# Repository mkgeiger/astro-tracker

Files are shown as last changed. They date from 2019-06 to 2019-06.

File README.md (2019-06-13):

# High precision Astro Tracker with wireless GOTO

## Overview

The inspiration of this project founded in the combination of my two hobbies: astronomy and microcontroller projects. This projects describes building an equatorial mount stepper motor controller with GPS high precision star-, moon- and sun-tracking. A wireless GOTO control via Skysafari App and a webinterface for individual stepper motor settings is also implemented. The features for my needs are:
* GPS timebase for high precision tracking
* tracking of rectascension in stellar, lunar, solar and user defined speeds
* north and south hemisphere support
* wireless GOTO over WIFI supporting LX200 protocol from the Skysafari App
* stepper motor control for rectascension and declination axis including fast slewing for GOTO
* LED indication of fast slewing in action
* individual stepper motor settings over a webpage presented by a webserver
* autoguider port
* 12V power supply

## Hardware

### NodeMCU ESP32

I decided to take this microcontroller board because of its high power with 2 cores, 4 fast high precision couters and easy programming, WIFI and small form factor. Following GPIOs are used:

  Signal          | ESP32
  ----------------|-----------
  RA_PHASE1..4    | GPIO12..15
  DEC_PHASE1..4   | GPIO16..19
  RA_LED          | GPIO0
  DEC_LED         | GPIO4
  STATUS_LED      | GPIO2
  ONE_PPS         | GPIO21
  AUTOGUIDE_RA_M  | GPIO26
  AUTOGUIDE_RA_P  | GPIO27
  AUTOGUIDE_DEC_M | GPIO32
  AUTOGUIDE_DEC_P | GPIO33
  
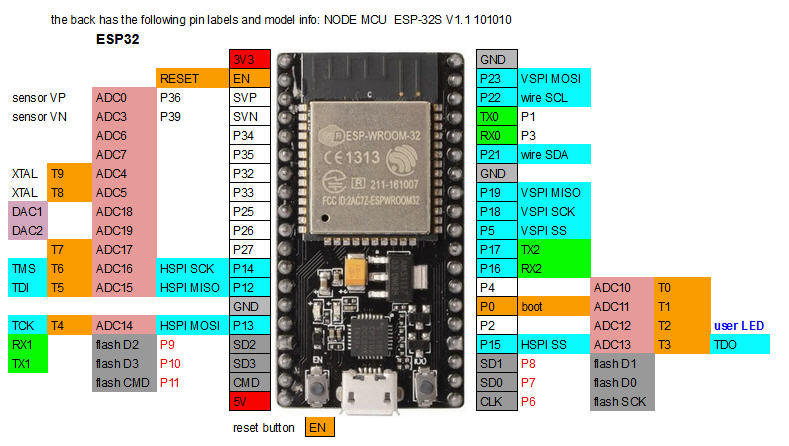
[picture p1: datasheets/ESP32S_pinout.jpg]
ESP32 NodeMCU
This module can be obtained at Ebay for about 5€. 

### GPS receiver Navilock EM406A

For calibrating the CPU frequency to less than 1ppm a high precision timebase is needed. The most accurate timebase which a normal person can get is from GPS. Some of these embedded GPS devices feed out a 1PPS (pulse per second) pin. This pin delivers a high accurate pulse per second with extremely low jitter. For this project only this pin is used for CPU counters calibration. The UART pins are connected and can be used for upcoming features. The datasheet for the EM406A can be found [here](/datasheets/EM406A_User_Manual.pdf).

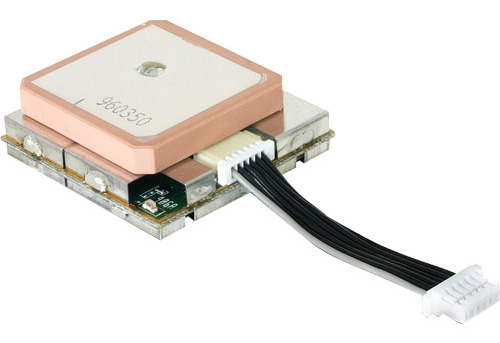
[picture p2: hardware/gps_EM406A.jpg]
gps_EM406A


### Stepper motor controller

The TB6612FNG is a great motor driver that is perfect for interfacing a single bipolar/unipolar stepper motor. The MOSFET-based H-bridges are much more efficient than the BJT-based H-bridges used in older drivers such as the L298N, which allows more current to be delivered to the motors and less to be drawn from the logic supply. This little breakout board gives direct access to all of the features of the TB6612FNG and adds power supply capacitors and reverse battery protection on the motor supply.

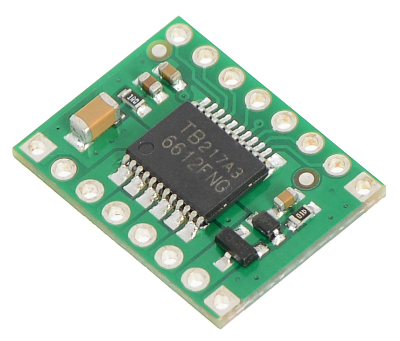
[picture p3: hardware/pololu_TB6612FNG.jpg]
pololu_TB6612FNG


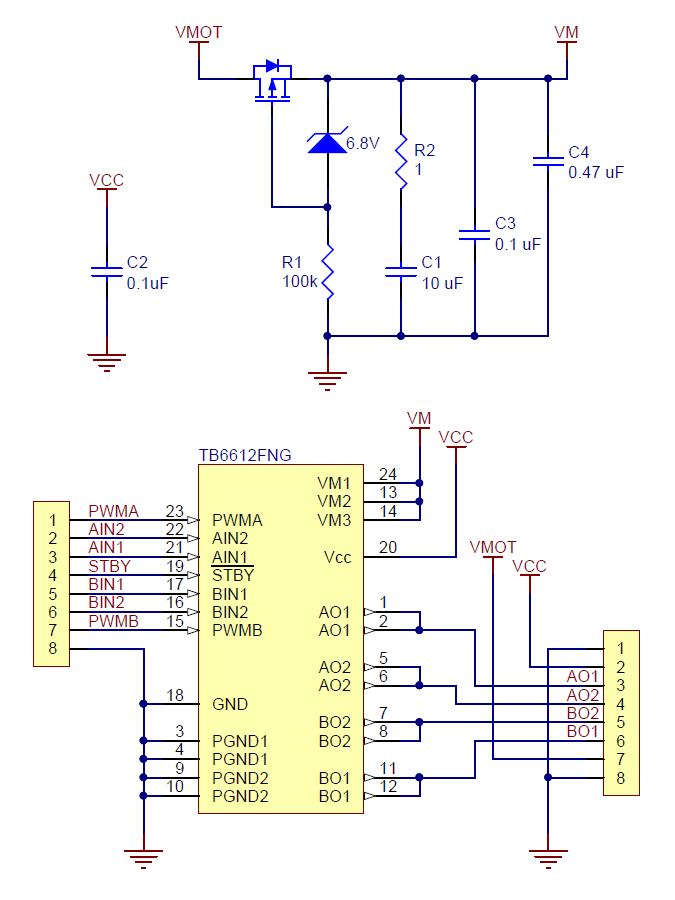
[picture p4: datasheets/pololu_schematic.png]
pololu_schematic


### Vixen MT-1 stepper motor

In my mount (Vixen GP) two of these motors are used for rectascension and declination. This stepper motor has following data:
* motor max speed factor: 32
* motor steps per full turn: 48
* gear box ratio: 1:120
* worm wheel ratio (Vixen GP mount): 1:144

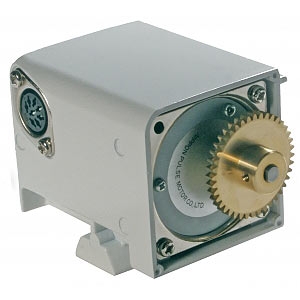
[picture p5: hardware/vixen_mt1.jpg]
vixen_mt1


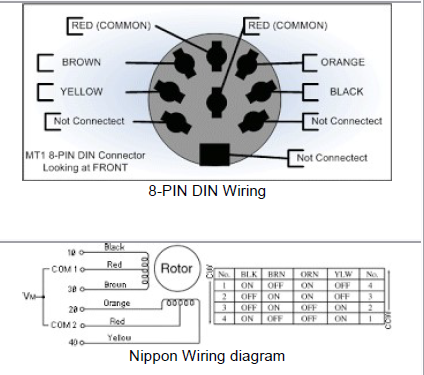
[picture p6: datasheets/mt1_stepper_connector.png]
mt1_stepper_connector


### Bosch VMB 12V stepper motor

For an other mount (EQ3) this motor is used only for rectascension. This stepper motor has following data:
* motor max speed factor: 32
* motor steps per full turn: 24
* gear box ratio: 384:116375
* worm wheel ratio (EQ3 mount): 1:138

### Power supply unit

This DC/DC converter is a cheap step down module based on the LM2596 chip. This module can be obtained at Ebay for about 1€. The input voltage depends on the stepper motors, for the Vixen MT-1 motors it is 12V. The output voltage has to be trimmed to 5V.

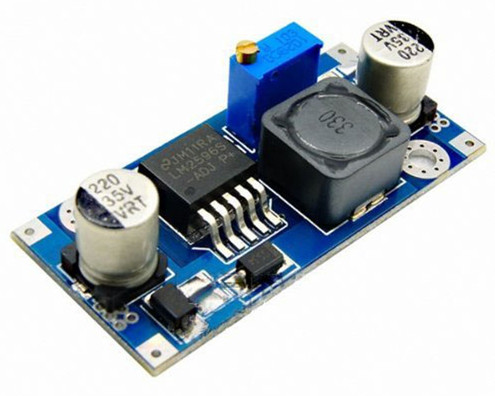
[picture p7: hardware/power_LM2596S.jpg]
power_LM2596S


### Connectors

#### Stepper motors (SUB-D 15)

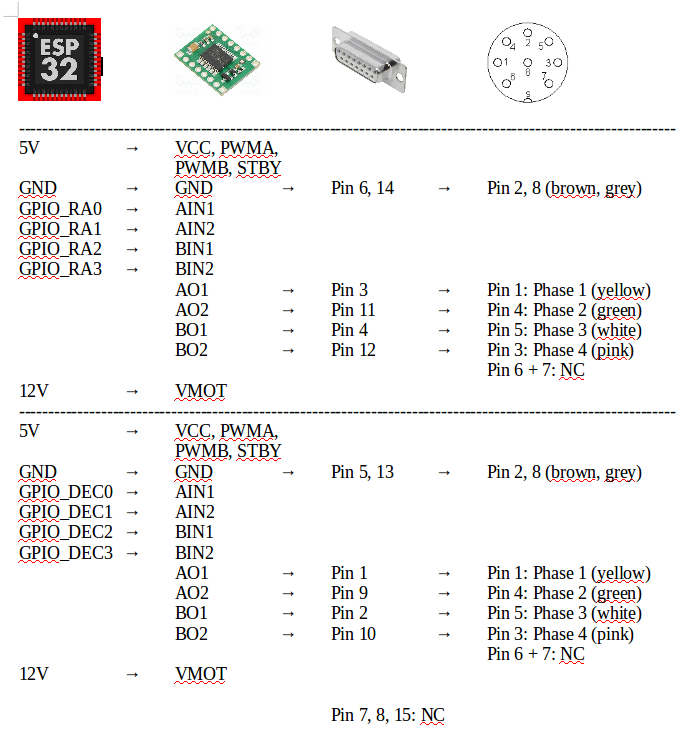
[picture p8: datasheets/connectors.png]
connectors


#### Autoguider port ST-4 (RJ-11/12)

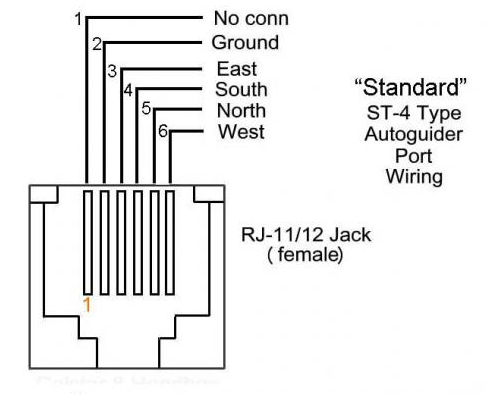
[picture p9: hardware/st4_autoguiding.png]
st4_autoguiding


### PCB layout

The PCB layout is created with Eagle Autorouter in a way to place all modules mentioned above near to each other on a single PCB. The Eagle PCB file can be downloaded from [here](/hardware/astrotracker.brd).

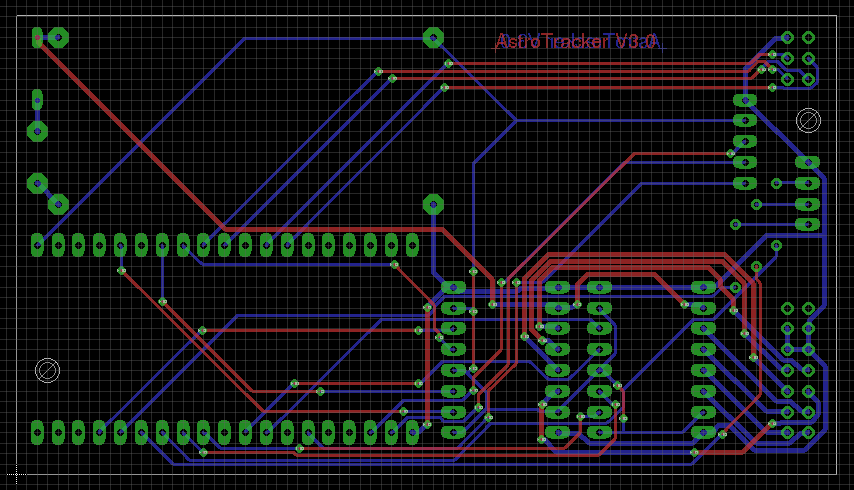
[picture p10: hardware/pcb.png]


## [Software](/AstroTracker/AstroTracker.ino)

### Initialization

#### Shared memory between tasks

For this purpose a mutex semaphore is created.

#### Exchanging data between tasks on different cores

For sending LX200 messages to the process task a message queue is created.

#### GPIOs

Most pins are configured as output pins, except the autoguiding and the 1PPS pin. These are configured respectively as input pins with pullups and as interrupt pin.

#### Non volatile memory

All configured motor-, gear- and speed-parameters are read during every startup.

#### High precision HW counters frequency measurement

At every startup the clock frequency of the four 64-bit HW counters is measured. This is done with help of the 1PPS pulse from the GPS module. Every precise second (1ppm jitter) the counter values are read out to determine the counting frequency. 10 values are taken to calculate the average counting frequency. This value is taken to calculate the exact parameterisation of the different stepping speeds.

#### Timers

For reaching the highest precision in tracking all four 64-bit timers are used. 
For further information see chapter [Interrupts].

#### Parameterisation

For the parameterisation the values from the non volatile memory (motor-, gear- and speed parameters) and the determined counting clock frequency are used for calculating the different stepping speeds.

#### WIFI

WIFI is initialized as an access point to be able to connect with a mobile phone also without an existing network in the field. The access parameters are: IP: 192.168.4.1, SSID: ASTRO_TRACKER, Password: see source code (default: xxxxxxxx).

### Tasks

The overall architecture splits the SW into two parts running on the two independant CPU cores. I decided to run the server tasks on core 0 (Pro CPU) and the time critical tasks and interrupts on core 1 (App CPU). 

#### LX200 server task (core 0, low priority)

This tasks implements a WIFI server to accept LX200 commands from a Sky Safari client, like a mobile phone with Sky Safari for Android. Sky Safari does not make a persistent connection, so each command query is managed as a single independent client. Only the LX200 commands (like GOTO, ALIGN, STOP, etc.) which are sent by Sky Safari are supported actually. The commands are parsed to extract informations like coordinates which are sent via message queue to the "Process Commands" task running on core 0. The northern or southern hemisphere parameter is determined by the "current site latitude" LX200 command.

#### Web server task (core 0, high priority)

This task offers a webpage to any client. In a webbowser the user can configure the individual parameters of the stepper motors, like steps per rotation and maximum speed factor. Also the gear and worm wheel ratio can be configured. Also the user has the posibility to choose the tracking speed of the rectascenson axis. All these parameters are stored in a non volatile memory to be present with the next boot of the system.

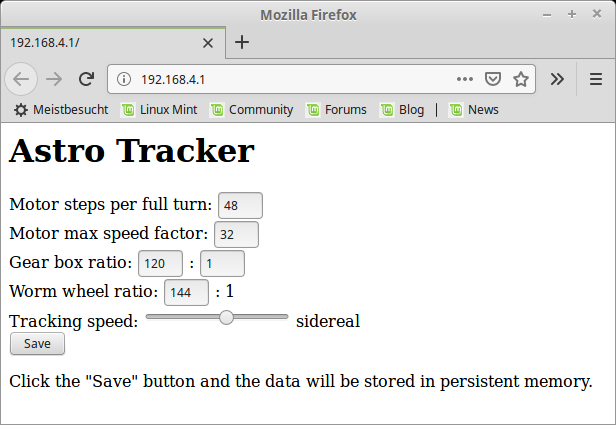
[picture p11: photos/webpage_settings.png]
webpage


#### Process commands task(core 1, high priority)

This task is responsible for receiving the parsed LX200 commands and for calculating the stepping control parameters for the stepper motors, like stepping speed, direction up/down and left/right and the number of steps for fast foreward/backward slewing (GOTO). For determining the fast foreward/backward steps in rectascension direction, the time for slewing to the destination object and the rotation of the earth around the rectascension axis are considered in the calculation formulas.

#### Current position task (core 1, low priority)

This task is responsible for sending the actual position (rectascension and declination) back to the Sky Safari client. Sky Safari uses this information to draw a crosshair on the sky where the telescope is pointing to. An update of this information is sent every 100ms.

#### Autoguider task (core 1, loop(), very low priority)

This task checks continuously the autoguider ports to correct the deviation with 0.5x speed in DEC-, DEC+, RA- direction and 1.5x speed in RA+ direction. Apart from this this task is also responsible to let the alive LED blink with 1Hz.

### Interrupts

#### 1 PPS interrupts

This interrupt is triggered every second by the GPS module. It used initially for calibrating the high resolution counters. At startup 10 samples of counter values are taken every second to calculate the average counting frequency. This is needed to reach a high accuracy.

#### Normal speed timer interrupt

This timer is programmed to come for every single full step for the rectascension stepper motor when tracking is active. Tracking speeds can be stellar, lunar, solar and various user defined speeds.

#### Fast speed timer interrupt

This timer is programmed to come for every single full step for both rectascension and declination stepper motors when the user presses the up/down/left/right buttons or when slewing to a destination object is currently active (GOTO). The slewing speed is the maximum possible speed for the motors, in case of MT-1 motors it is 32x.

#### Correction RA+ interrupt

This timer is programmed to come for positive rectascension autoguiding corrections. The speed is then with factor 1.5x.

#### Correction RA-, DEC-, DEC+ interrupt

This timer is programmed to come for negative rectascension, negativ- and positive declination autoguiding corrections. The speed is then with factor 0.5x.

## Photos

Assembled PCB:
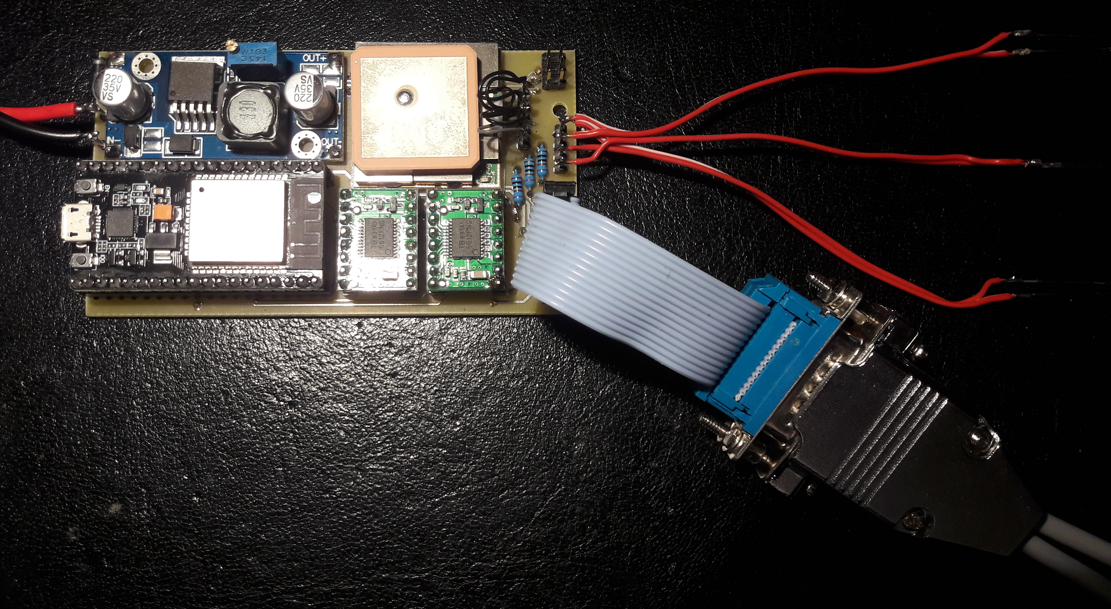
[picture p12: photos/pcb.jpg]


Opened case:
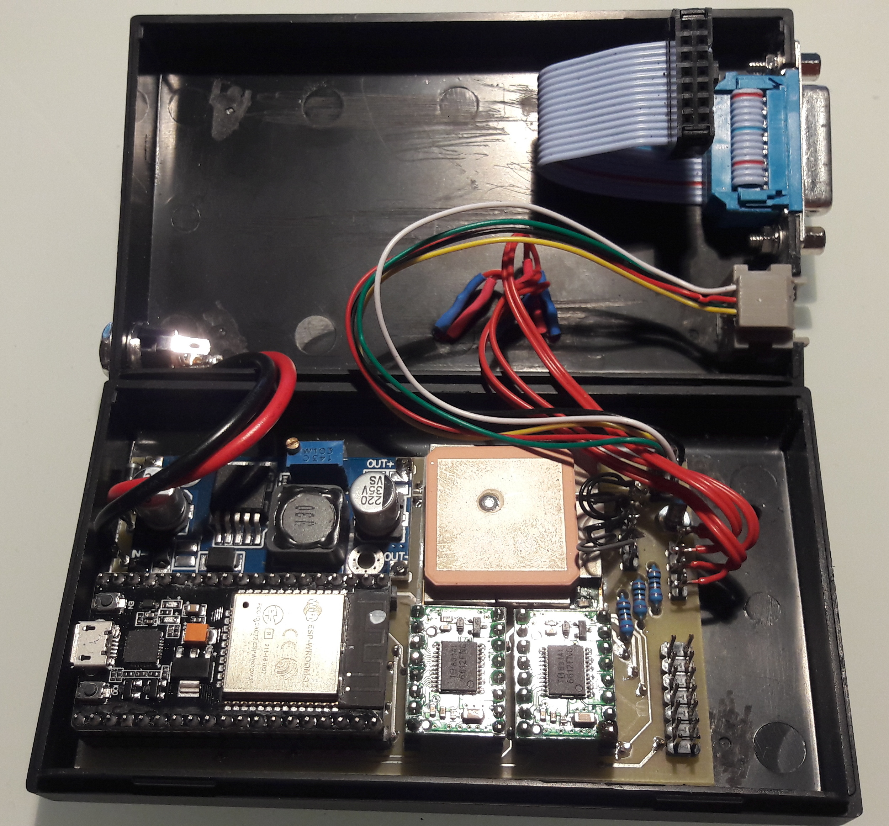
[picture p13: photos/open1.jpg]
open1


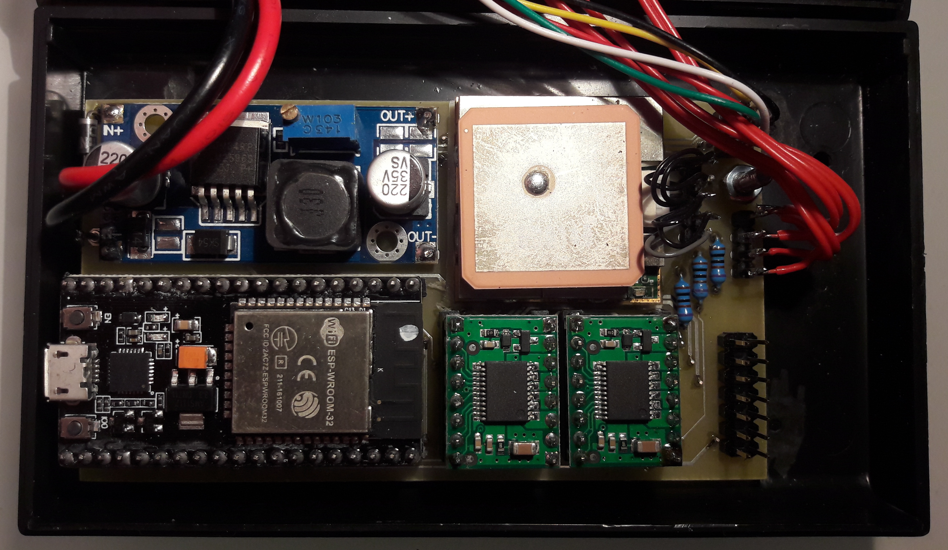
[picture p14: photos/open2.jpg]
open2


Finished device:
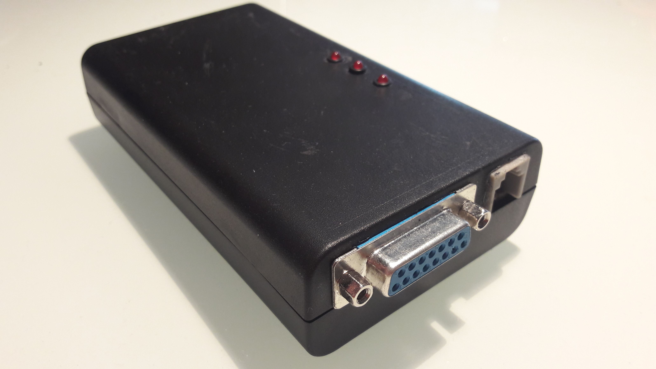
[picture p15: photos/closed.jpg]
closed


System view (incl. Vixen GP mount):
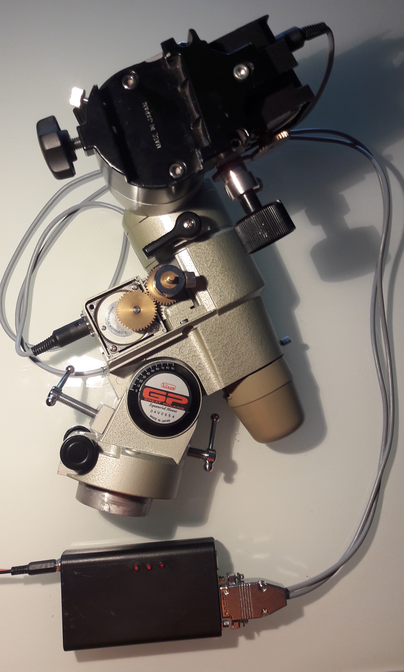
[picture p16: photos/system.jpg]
system


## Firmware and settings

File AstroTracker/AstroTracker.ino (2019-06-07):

/*=============================================================================
=======                            INCLUDES                             =======
=============================================================================*/
#include <WiFi.h>
#include <WiFiClient.h>
#include <WebServer.h>
#include <Preferences.h>

/*=============================================================================
=======                        DEFINES & MACROS                         =======
=============================================================================*/
#define USE_GPS_MODULE

// day rotation times [ms]
#define SPEED_0_5X   172800000ul
#define LUNAR_DAY     89428329ul
#define SOLAR_DAY     86400000ul
#define SIDEREAL_DAY  86164091ul
#define SPEED_1_5X    57600000ul
#define SPEED_2X      43200000ul
#define SPEED_4X      21600000ul

// arc seconds
#define RA_SECONDS_360   (24ul * 60ul * 60ul)  //   86400 sec
#define DEC_SECONDS_90   (90ul * 60ul * 60ul)  //  324000 sec
#define DEC_SECONDS_270 (270ul * 60ul * 60ul)  //  972000 sec
#define DEC_SECONDS_360 (360ul * 60ul * 60ul)  // 1296000 sec

// gpios
#define STATUS_LED_PIN     2
#define RA_LED_PIN         0
#define DEC_LED_PIN        4
#define RA_PHASE1_PIN     12
#define RA_PHASE2_PIN     13
#define RA_PHASE3_PIN     14
#define RA_PHASE4_PIN     15
#define DEC_PHASE1_PIN    16
#define DEC_PHASE2_PIN    17
#define DEC_PHASE3_PIN    18
#define DEC_PHASE4_PIN    19
#define ONE_PPS_PIN       21
#define UART1_RX_PIN      22
#define UART1_TX_PIN      23
#define AUTOGUIDE_RA_M    26
#define AUTOGUIDE_RA_P    27
#define AUTOGUIDE_DEC_M   32
#define AUTOGUIDE_DEC_P   33

// CPU cores
#define CORE_PRO_CPU  0
#define CORE_APP_CPU  1

// task priorities and stack size
#define TASK_LOW_PRIO   2
#define TASK_HIGH_PRIO  3
#define TASK_STACK_SIZE 0x1000

// other
#define MAX_CLIENTS          3
#define ONE_PPS_SAMPLES      12
#define WEBPAGE_BUFFER_SIZE  3500

/*=============================================================================
=======                        CONSTANTS & TYPES                        =======
=============================================================================*/
const char* ssid     = "ASTRO_TRACKER";
const char* password = "xxxxxxxx";

typedef struct
{
	boolean  ra_fast_tracking;
	uint8_t  ra_step;
	uint32_t ra_old;
	uint32_t ra_new;
	uint32_t ra_actual;
	uint32_t ra_steps;
	uint32_t ra_steps_total;
	uint8_t  ra_dir;
	uint8_t  ra_east;
	uint8_t  ra_west;
	uint8_t  ra_speed;         // 0 - off, 1 - sidereal, 2 - solar, 3 - lunar
	boolean  ra_corr_m;
	boolean  ra_corr_p;
	boolean  dec_fast_tracking;
	uint8_t  dec_step;
	uint32_t dec_old;
	uint32_t dec_new;
	uint32_t dec_actual;
	uint32_t dec_steps;
	uint32_t dec_steps_total;
	uint8_t  dec_dir;
	uint8_t  dec_north;
	uint8_t  dec_south;
	uint8_t  dec_speed;       // 0 - off, 1 - on
	boolean  dec_corr_m;
	boolean  dec_corr_p;
} radec_t;

/*=============================================================================
=======                VARIABLES & MESSAGES & RESSOURCEN                =======
=============================================================================*/
// non-volatile memory
static Preferences prefs;

// timers with timer critical section
static hw_timer_t *timer_normal  = NULL;
static hw_timer_t *timer_fast    = NULL;
static hw_timer_t *timer_corr[2] = {NULL};
static portMUX_TYPE timerMux = portMUX_INITIALIZER_UNLOCKED;
static uint64_t counter_normal;
static uint64_t counter_fast;
static uint64_t counter_corr[2];

// mutex for shared memory between tasks
static SemaphoreHandle_t sem_mutex;

// message queue between tasks
static QueueHandle_t msg_queue;
static char msg_buf[22];

// server stuff
static WebServer  webserver(80);
static WiFiServer lx200server(4030);

// frequency measurement
static volatile uint8_t  one_pps_sample_idx = 0;
static volatile uint64_t one_pps_samples[ONE_PPS_SAMPLES];
static uint64_t measured_frequency;

// current position, which is sent cyclic to the client
static char cur_pos_ra[9];
static char cur_pos_dec[10];

// parameterisation                                  |  Vixen MT-1 12V + GP | Bosch VMB 12V + EQ3
//---------------------------------------------------+----------------------+---------------------
static uint16_t mms;    // motor max speed factor    |                   32 |                  32
static uint16_t mst;    // motor steps per full turn |                   48 |                  24
static uint32_t gdd;    // gear box dividend         |                    1 |                 384
static uint32_t gdr;    // gear box divisor          |                  120 |              116375
static uint16_t wwr;    // worm wheel ratio          |                  144 |                 138

static uint32_t day_ms[8] = {SIDEREAL_DAY, SPEED_0_5X, LUNAR_DAY, SOLAR_DAY, SIDEREAL_DAY,  SPEED_1_5X, SPEED_2X, SPEED_4X};

// math stuff
static volatile uint8_t hemisphere = 0;  // 0 - northern hemisphere, 1 - southern hemisphere
static volatile radec_t radec;
static uint32_t ra_steps_360;
static uint32_t dec_steps_360;
static unsigned long time_now;

/*=============================================================================
=======                    PROTOTYPES OF PRIVATE METHODS                =======
=============================================================================*/
static void     web_server_task(void *parameter);
static void     lx200_server_task(void *parameter);
static void     process_commands_task(void *parameter);
static void     current_pos_task(void *parameter);
static void     httpHandleRoot(void);
static void     parseCommand(char *req, char *resp);
static uint64_t calcAverageFrequency(void);
static void     calcParameterisation(void);
static void     calcRA2steps(void);
static void     calcDEC2steps(void);
static void     calcSteps2RA(uint32_t steps, uint32_t *ra);
static void     calcSteps2DEC(uint32_t steps, uint32_t *dec);
static uint32_t stringToUnsigned(uint8_t *buf, uint8_t len);
static void     stopSlewing(void);
static void     gotoPosition(uint8_t *buf);
static void     alignPosition(uint8_t *buf);
static void     evalAutoguidePins(void);

/*=============================================================================
=======                               METHODS                           =======
=============================================================================*/
// 1.5x correction slewing (for RA+)
void IRAM_ATTR onTimerCorr0()
{
	if ((radec.ra_corr_p == true) && (radec.ra_fast_tracking == false))
	{
		// RA motor off
		REG_WRITE(GPIO_OUT_W1TC_REG, 0xful << RA_PHASE1_PIN);
		if (radec.ra_speed > 0)
		{
			if (hemisphere == 0)
			{
				radec.ra_step ++;
			}
			else
			{
				radec.ra_step --;
			}
			REG_WRITE(GPIO_OUT_W1TS_REG, 1ul << ((radec.ra_step & 0x03) + RA_PHASE1_PIN));
		}
		// RA led on
		digitalWrite(RA_LED_PIN, HIGH);
	}
}

// 0.5x correction slewing (for RA-, Dec- and Dec+)
void IRAM_ATTR onTimerCorr1()
{
	if ((radec.ra_corr_m == true) && (radec.ra_fast_tracking == false))
	{
		// RA motor off
		REG_WRITE(GPIO_OUT_W1TC_REG, 0xful << RA_PHASE1_PIN);
		if (radec.ra_speed > 0)
		{
			if (hemisphere == 0)
			{
				radec.ra_step ++;
			}
			else
			{
				radec.ra_step --;
			}
			REG_WRITE(GPIO_OUT_W1TS_REG, 1ul << ((radec.ra_step & 0x03) + RA_PHASE1_PIN));
		}
		// RA led on
		digitalWrite(RA_LED_PIN, HIGH);
	}

	if ((radec.dec_corr_m == true) && (radec.dec_fast_tracking == false))
	{
		// DEC motor off
		REG_WRITE(GPIO_OUT_W1TC_REG, 0xful << DEC_PHASE1_PIN);
		if (radec.dec_speed > 0)
		{
			if (hemisphere == 0)
			{
				// slew down
				radec.dec_step --;
			}
			else
			{
				// slew up
				radec.dec_step ++;
			}
			REG_WRITE(GPIO_OUT_W1TS_REG, 1ul << ((radec.dec_step & 0x03) + DEC_PHASE1_PIN));
		}
		// DEC led on
		digitalWrite(DEC_LED_PIN, HIGH);
	}

	if ((radec.dec_corr_p == true) && (radec.dec_fast_tracking == false))
	{
		// DEC motor off
		REG_WRITE(GPIO_OUT_W1TC_REG, 0xful << DEC_PHASE1_PIN);
		if (radec.dec_speed > 0)
		{
			if (hemisphere == 0)
			{
				// slew down
				radec.dec_step ++;
			}
			else
			{
				// slew up
				radec.dec_step --;
			}
			REG_WRITE(GPIO_OUT_W1TS_REG, 1ul << ((radec.dec_step & 0x03) + DEC_PHASE1_PIN));
		}
		// DEC led on
		digitalWrite(DEC_LED_PIN, HIGH);
	}
}

// normal slewing (only RA) interrupt service routine
void IRAM_ATTR onTimerNormal()
{
	if ((radec.ra_corr_m == false) && (radec.ra_corr_p == false) && (radec.ra_fast_tracking == false))
	{
		// RA motor off
		REG_WRITE(GPIO_OUT_W1TC_REG, 0xful << RA_PHASE1_PIN);
		if (radec.ra_speed > 0)
		{
			if (hemisphere == 0)
			{
				radec.ra_step ++;
			}
			else
			{
				radec.ra_step --;
			}
			REG_WRITE(GPIO_OUT_W1TS_REG, 1ul << ((radec.ra_step & 0x03) + RA_PHASE1_PIN));
		}
		// RA led off
		digitalWrite(RA_LED_PIN, LOW);
	}
}

// fast slewing interrupt service routine
void IRAM_ATTR onTimerFast()
{
	if (radec.ra_fast_tracking == true)
	{
		// RA motor off
		REG_WRITE(GPIO_OUT_W1TC_REG, 0xful << RA_PHASE1_PIN);
		if (radec.ra_east == 1)
		{
			if (hemisphere == 0)
			{
				// slew left
				radec.ra_step --;
			}
			else
			{
				// slew right
				radec.ra_step ++;
			}
			REG_WRITE(GPIO_OUT_W1TS_REG, 1ul << ((radec.ra_step & 0x03) + RA_PHASE1_PIN));
		}
		else if (radec.ra_west == 1)
		{
			if (hemisphere == 0)
			{
				// slew right
				radec.ra_step ++;
			}
			else
			{
				// slew left
				radec.ra_step --;
			}
			REG_WRITE(GPIO_OUT_W1TS_REG, 1ul << ((radec.ra_step & 0x03) + RA_PHASE1_PIN));
		}
		else if ((radec.ra_steps > 0ul) && (radec.ra_speed > 0))
		{
			if ((radec.ra_dir ^ hemisphere) == 0)
			{
				// slew left
				radec.ra_step --;
			}
			else
			{
				// slew right
				radec.ra_step ++;
			}
			REG_WRITE(GPIO_OUT_W1TS_REG, 1ul << ((radec.ra_step & 0x03) + RA_PHASE1_PIN));
			radec.ra_steps --;
			if (radec.ra_steps == 0ul)
			{
				radec.ra_actual = radec.ra_new;
				radec.ra_old = radec.ra_new;
				radec.ra_fast_tracking = false;
			}
			// RA led on
			digitalWrite(RA_LED_PIN, HIGH);
		}
		else
		{
			// RA led off
			digitalWrite(RA_LED_PIN, LOW);
		}
	}

	if (radec.dec_fast_tracking == true)
	{
		// DEC motor off
		REG_WRITE(GPIO_OUT_W1TC_REG, 0xful << DEC_PHASE1_PIN);
		if (radec.dec_north == 1)
		{
			if (hemisphere == 0)
			{
				// slew up
				radec.dec_step ++;
			}
			else
			{
				// slew down
				radec.dec_step --;
			}
			REG_WRITE(GPIO_OUT_W1TS_REG, 1ul << ((radec.dec_step & 0x03) + DEC_PHASE1_PIN));
		}
		else if (radec.dec_south == 1)
		{
			if (hemisphere == 0)
			{
				// slew down
				radec.dec_step --;
			}
			else
			{
				// slew up
				radec.dec_step ++;
			}
			REG_WRITE(GPIO_OUT_W1TS_REG, 1ul << ((radec.dec_step & 0x03) + DEC_PHASE1_PIN));
		}
		else if ((radec.dec_steps > 0ul) && (radec.dec_speed > 0))
		{
			if ((radec.dec_dir ^ hemisphere) == 0)
			{
				// slew down
				radec.dec_step --;
			}
			else
			{
				// slew up
				radec.dec_step ++;
			}
			REG_WRITE(GPIO_OUT_W1TS_REG, 1ul << ((radec.dec_step & 0x03) + DEC_PHASE1_PIN));

			radec.dec_steps --;
			if (radec.dec_steps == 0ul)
			{
				radec.dec_actual = radec.dec_new;
				radec.dec_old = radec.dec_new;
				radec.dec_fast_tracking = false;
			}
			// DEC led on
			digitalWrite(DEC_LED_PIN, HIGH);
		}
		else
		{
			// DEC led off
			digitalWrite(DEC_LED_PIN, LOW);
		}
	}
  else
  {
      // DEC led off
      digitalWrite(DEC_LED_PIN, LOW);    
  }
}

// 1PPS interupt service routine
void IRAM_ATTR handleOnePPSinterrupt()
{
	// with each second take a counter sample
	if (one_pps_sample_idx < ONE_PPS_SAMPLES)
	{
		one_pps_samples[one_pps_sample_idx ++] = timerRead(timer_normal);
	}
}

static uint64_t calcAverageFrequency(void)
{
	uint64_t average = 0ull;

	// start free running 64 bit counter with max. frequency (= 40MHz)
	timer_normal = timerBegin(0, 2, true);

	// configure Pin as Interrupt pin, falling edge, internal pull-up
	pinMode(ONE_PPS_PIN, INPUT_PULLUP);
	attachInterrupt(digitalPinToInterrupt(ONE_PPS_PIN), handleOnePPSinterrupt, FALLING);

	// wait until all counter samples were taken
	while (one_pps_sample_idx < ONE_PPS_SAMPLES);

	// sampling done, detach from interrupt and stop the counter
	detachInterrupt(digitalPinToInterrupt(ONE_PPS_PIN));
	timerEnd(timer_normal);

	// calculate the average counter frequency
	for (one_pps_sample_idx = 1; one_pps_sample_idx < (ONE_PPS_SAMPLES - 1); one_pps_sample_idx ++)
	{
		average += (one_pps_samples[one_pps_sample_idx + 1] - one_pps_samples[one_pps_sample_idx]);
	}

	// rounding
	average += ((ONE_PPS_SAMPLES - 2) / 2);

	// average
	average /= (ONE_PPS_SAMPLES - 2);

	return average;
}

static void parseCommand(char *req, char *resp)
{
	static char tgt_pos_ra[9];
	static char tgt_pos_dec[10];

	if ((NULL != req) && (NULL != resp))
	{
		// :GR# Get telescope right ascension (RA).
		if (0 == strcmp (":GR#", req))
		{
			xSemaphoreTake( sem_mutex, portMAX_DELAY );
			sprintf (resp, "%s#", cur_pos_ra);
			xSemaphoreGive( sem_mutex );
		}
		// :GD# Get telescope declination (DEC).
		if (0 == strcmp (":GD#", req))
		{
			xSemaphoreTake( sem_mutex, portMAX_DELAY );
			sprintf (resp, "%s#", cur_pos_dec);
			xSemaphoreGive( sem_mutex );
		}
		// :SrHH:MM:SS# Set target object right ascension (RA).
		if (0 == strncmp (":Sr", req, 3))
		{
			memcpy (tgt_pos_ra, &req[3], 8);
			tgt_pos_ra[8] = 0;
			strcpy (resp, "1");
		}
		// :SdsDD*MM:SS# Set target object declination (DEC).
		if (0 == strncmp (":Sd", req, 3))
		{
			memcpy (tgt_pos_dec, &req[3], 9);
			tgt_pos_dec[9] = 0;
			strcpy (resp, "1");
		}
		// :CM# Synchronizes the telescope's position with the currently selected database object's coordinates.
		if (0 == strcmp (":CM#", req))
		{
			sprintf(msg_buf, ":CM%s%s#", tgt_pos_ra, tgt_pos_dec);
			xQueueSend( msg_queue, msg_buf, portMAX_DELAY );
			strcpy (resp, "#");
		}
		// :MS# Slew to target object
		if (0 == strcmp (":MS#", req))
		{
			sprintf(msg_buf, ":MS%s%s#", tgt_pos_ra, tgt_pos_dec);
			xQueueSend( msg_queue, msg_buf, portMAX_DELAY );
			strcpy (resp, "0");
		}
		// :StsDD*MM# Set the current site latitude.
		if (0 == strncmp (":St", req, 3))
		{
			strcpy(msg_buf, req);
			xQueueSend( msg_queue, msg_buf, portMAX_DELAY );
			strcpy (resp, "1");
		}
		// :SgDDD*MM# Set current site’s longitude.
		if (0 == strncmp (":Sg", req, 3))
		{
			strcpy (resp, "1");
		}
		// :SGsHH.H# Set the number of hours added to local time to yield UTC.
		if (0 == strncmp (":SG", req, 3))
		{
			strcpy (resp, "1");
		}
		// :SLHH:MM:SS# Set the local time.
		if (0 == strncmp (":SL", req, 3))
		{
			strcpy (resp, "1");
		}
		// :SCMM/DD/YY# Change handbox date.
		if (0 == strncmp (":SC", req ,3))
		{
			strcpy (resp, "1Updating Planetary Data       #                              #");
		}
		// :Q# Halt all current slewing.
		if (0 == strcmp (":Q#", req))
		{
			strcpy(msg_buf, ":Q#");
			xQueueSend( msg_queue, msg_buf, portMAX_DELAY );
			//Serial.println("Stop slewing");
			resp[0] = 0;
		}
		// :Me# Move telescope east at current slew rate.
		if (0 == strcmp (":Me#", req))
		{
			strcpy(msg_buf, ":Me#");
			xQueueSend( msg_queue, msg_buf, portMAX_DELAY );
			resp[0] = 0;
		}
		// :Mn# Move telescope north at current slew rate.
		if (0 == strcmp (":Mn#", req))
		{
			strcpy(msg_buf, ":Mn#");
			xQueueSend( msg_queue, msg_buf, portMAX_DELAY );
			resp[0] = 0;
		}
		// :Ms# Move telescope south at current slew rate.
		if (0 == strcmp (":Ms#", req))
		{
			strcpy(msg_buf, ":Ms#");
			xQueueSend( msg_queue, msg_buf, portMAX_DELAY );
			resp[0] = 0;
		}
		// :Mw# Move telescope west at current slew rate.
		if (0 == strcmp (":Mw#", req))
		{
			strcpy(msg_buf, ":Mw#");
			xQueueSend( msg_queue, msg_buf, portMAX_DELAY );
			resp[0] = 0;
		}
		// :Qe# Halt eastward slews.
		if (0 == strcmp (":Qe#", req))
		{
			strcpy(msg_buf, ":Qe#");
			xQueueSend( msg_queue, msg_buf, portMAX_DELAY );
			resp[0] = 0;
		}
		// :Qn# Halt northward slews.
		if (0 == strcmp (":Qn#", req))
		{
			strcpy(msg_buf, ":Qn#");
			xQueueSend( msg_queue, msg_buf, portMAX_DELAY );
			resp[0] = 0;
		}
		// :Qs# Halt southward slews.
		if (0 == strcmp (":Qs#", req))
		{
			strcpy(msg_buf, ":Qs#");
			xQueueSend( msg_queue, msg_buf, portMAX_DELAY );
			resp[0] = 0;
		}
		// :Qw# Halt westward slews.
		if (0 == strcmp (":Qw#", req))
		{
			strcpy(msg_buf, ":Qw#");
			xQueueSend( msg_queue, msg_buf, portMAX_DELAY );
			resp[0] = 0;
		}
		// :RC# Set slew rate to centering rate (2nd slowest).
		if (0 == strcmp (":RC#", req))
		{
			resp[0] = 0;
		}
		// :RG# Set slew rate to guiding rate (slowest).
		if (0 == strcmp (":RG#", req))
		{
			resp[0] = 0;
		}
		// :RM# Set slew rate to find rate (2nd fastest).
		if (0 == strcmp (":RM#", req))
		{
			resp[0] = 0;
		}
		// :RS# Set slew rate to max (fastest).
		if (0 == strcmp (":RS#", req))
		{
			resp[0] = 0;
		}
	}
}

static void lx200_server_task(void *parameter)
{
	static char request[50];
	static char response[200];
	static WiFiClient client[MAX_CLIENTS];
	int i;

	lx200server.begin();

	for(;;)
	{
		delay(25);

		// Sky Safari does not make a persistent connection, so each command query is managed as a single independent client
		if (lx200server.hasClient())
		{
			for (i = 0; i < MAX_CLIENTS; i++)
			{
				// client is trying to connect, find free/disconnected spot
				if (!client[i] || !client[i].connected())
				{
					if (client[i])
					{
						// disconnect client
						client[i].stop();
					}
					client[i] = lx200server.available();
				}
			}
		}

		// check clients for data
		for (i = 0; i < MAX_CLIENTS; i++)
		{
			if (client[i] && client[i].connected())
			{
				// get data from the client
				while (client[i].available())
				{
					int n = client[i].available();
					client[i].readBytes(request, n);
					request[n] = 0;
					parseCommand(request, response);
					if (0 < strlen(response))
					{
						client[i].write(response, strlen(response));
					}
				}
			}
		}
	}
}

static void calcRA2steps(void)
{
	uint32_t steps1, steps2, steps_total1, steps_total2;
	uint8_t dir1, dir2;

	xSemaphoreTake( sem_mutex, portMAX_DELAY );
	if (radec.ra_new >= radec.ra_old)
	{
		// northern hemisphere: left, southern hemisphere: right
		steps1 = (((uint64_t)(radec.ra_new - radec.ra_old)) * ra_steps_360) / RA_SECONDS_360;
		steps_total1 = steps1 - (steps1 * counter_fast) / (counter_normal + counter_fast);
		dir1 = 0;
		// northern hemisphere: right, southern hemisphere: left
		steps2 = ra_steps_360 - steps1;
		steps_total2 = steps2 + (steps2 * counter_fast) / (counter_normal - counter_fast);
		dir2 = 1;
	}
	else
	{
		// northern hemisphere: right, southern hemisphere: left
		steps1 = (((uint64_t)(radec.ra_old - radec.ra_new)) * ra_steps_360) / RA_SECONDS_360;
		steps_total1 = steps1 + (steps1 * counter_fast) / (counter_normal - counter_fast);
		dir1 = 1;
		// northern hemisphere: left, southern hemisphere: right
		steps2 = ra_steps_360 - steps1;
		steps_total2 = steps2 - (steps2 * counter_fast) / (counter_normal + counter_fast);
		dir2 = 0;
	}
	xSemaphoreGive( sem_mutex );

	portENTER_CRITICAL(&timerMux);
	if (steps_total1 < steps_total2)
	{
		radec.ra_steps = steps_total1;
		radec.ra_dir = dir1;
	}
	else
	{
		radec.ra_steps = steps_total2;
		radec.ra_dir = dir2;
	}
	radec.ra_steps_total = radec.ra_steps;
	if (radec.ra_steps > 0)
	{
		radec.ra_fast_tracking = true;
	}
	portEXIT_CRITICAL(&timerMux);
}

static void calcSteps2RA(uint32_t steps, uint32_t *ra)
{
	if (radec.ra_new >= radec.ra_old)
	{
		if (radec.ra_dir == 0)
		{
			*ra = radec.ra_old + (uint32_t)(((uint64_t)(radec.ra_steps_total - steps) * ((uint64_t)(radec.ra_new - radec.ra_old))) / ((uint64_t)radec.ra_steps_total));
		}
		else
		{
			*ra = (RA_SECONDS_360 + radec.ra_old - (uint32_t)(((uint64_t)(radec.ra_steps_total - steps) * ((uint64_t)(RA_SECONDS_360 - radec.ra_new + radec.ra_old))) / ((uint64_t)radec.ra_steps_total))) % RA_SECONDS_360;
		}
	}
	else
	{
		if (radec.ra_dir == 0)
		{
			*ra = (RA_SECONDS_360 + radec.ra_old + (uint32_t)(((uint64_t)(radec.ra_steps_total - steps) * ((uint64_t)(RA_SECONDS_360 - radec.ra_old + radec.ra_new))) / ((uint64_t)radec.ra_steps_total))) % RA_SECONDS_360;
		}
		else
		{
			*ra = radec.ra_old - (uint32_t)(((uint64_t)(radec.ra_steps_total - steps) * ((uint64_t)(radec.ra_old - radec.ra_new))) / ((uint64_t)radec.ra_steps_total));
		}
	}
}

static void calcDEC2steps(void)
{
	uint32_t steps_total;
	uint8_t dir;

	xSemaphoreTake( sem_mutex, portMAX_DELAY );
	if (radec.dec_new >= radec.dec_old)
	{
		if ((radec.dec_new >= DEC_SECONDS_270) && (radec.dec_old <= DEC_SECONDS_90))
		{
			// down
			steps_total = (((uint64_t)(DEC_SECONDS_360 - (radec.dec_new - radec.dec_old))) * dec_steps_360) / DEC_SECONDS_360;
			dir = 0;
		}
		else
		{
			// up
			steps_total = (((uint64_t)(radec.dec_new - radec.dec_old)) * dec_steps_360) / DEC_SECONDS_360;
			dir = 1;
		}
	}
	else
	{
		if ((radec.dec_new <= DEC_SECONDS_90) && (radec.dec_old >= DEC_SECONDS_270))
		{
			// up
			steps_total = (((uint64_t)(DEC_SECONDS_360 - (radec.dec_old - radec.dec_new))) * dec_steps_360) / DEC_SECONDS_360;
			dir = 1;
		}
		else
		{
			// down
			steps_total = (((uint64_t)(radec.dec_old - radec.dec_new)) * dec_steps_360) / DEC_SECONDS_360;
			dir = 0;
		}
	}
	xSemaphoreGive( sem_mutex );

	portENTER_CRITICAL(&timerMux);
	radec.dec_steps = steps_total;
	radec.dec_dir = dir;
	radec.dec_steps_total = radec.dec_steps;
	if (radec.dec_steps > 0)
	{
		radec.dec_fast_tracking = true;
	}
	portEXIT_CRITICAL(&timerMux);
}
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
void loop()
{
	static uint8_t val = HIGH;

	if ((millis() - time_now) > 500)
	{
		time_now = millis();
		val ^= 0x01;
		digitalWrite(STATUS_LED_PIN, val);
	}

	evalAutoguidePins();

#if 0
	int data;

	while (Serial1.available())
	{
		data = Serial1.read();
		Serial.write(data);
	}
#endif
}

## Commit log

2019-06-07 initial version
    [astrotracker.brd]
2019-06-09 Overview, ESP32, GPS
2019-06-10 added stepper motor controller chapter
2019-06-10 vixen_mt1 motor added
2019-06-10 Vixen MT-1 stepper motor chapter added
2019-06-13 Bosch VMB stepper motor added
